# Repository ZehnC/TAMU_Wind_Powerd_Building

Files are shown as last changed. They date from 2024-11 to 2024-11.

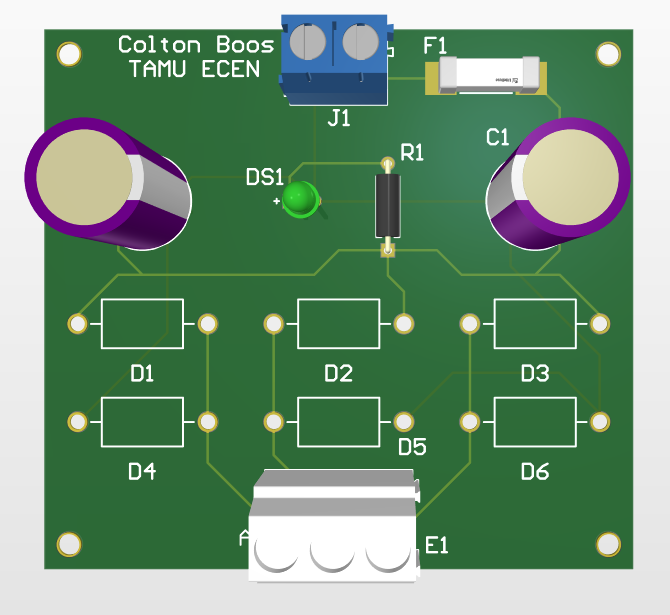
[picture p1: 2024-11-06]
RectifierPCB/rectifier_digital.PNG

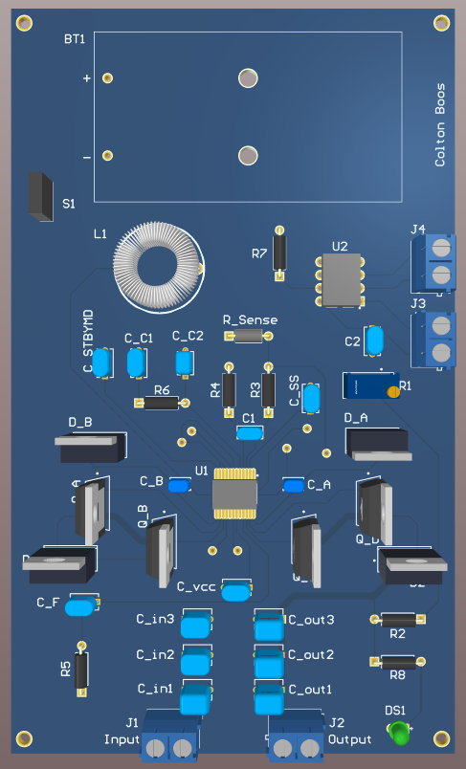
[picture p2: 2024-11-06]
BuckBoostConverterPCB/converter_digitalPCB.PNG

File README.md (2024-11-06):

# The-Wind-Powered-Building
Documentation and Files for the A&M Team 7 Wind-Powered-Building <br />
Team members include Colton Boos, Peter Zha, Reggie Sampson, and Maxwell Chen <br />
Sponsored by Dr. Wonhyeok Jang, with TA Rohith Ramanujam Kumar <br />

The wind-powered building is designed to deliver power from a small wind turbine to a residential home. The operation of the project consists of four main subsystems: the rectification and conversion subsystem, the switch controller subsystem, the inversion and conversion subsystem, and the monitor subsystem. These four systems working together converts three phase AC power to be stored in two batteries as DC power, which is then delivered to AC and DC loads. The amount of power generated and used is tracked by the monitor subsystem as well as battery capacity, and determines which battery to charge and which battery to discharge.
Due to issues with the wind turbine, our sponsor has given us approval to use an AC power supply as a substitute for demonstration. Hooking up the rectifier and converter to the input, the power input will be converted to DC power in order to charge the batteries. The microcontroller part of the monitor subsystem will automatically determine which battery needs to be charged. LED indicators inside the housing indicates which battery is charging and which battery is discharging. Power used from the batteries is delivered to two types of loads: an AC and DC load. The DC load is the LEDs mounted on the outside of the box. The AC load is directly next to the DC load, represented by a power outlet. The LEDs can be turned on and off and various loads can be plugged into the outlet.

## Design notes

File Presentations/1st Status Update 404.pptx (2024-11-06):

## Team 7: Wind-Powered Building Team Members: Colton, Reginald, Maxwell, Peter Sponsor: Dr. Jang TA: Rohith Ramanujam Kumar

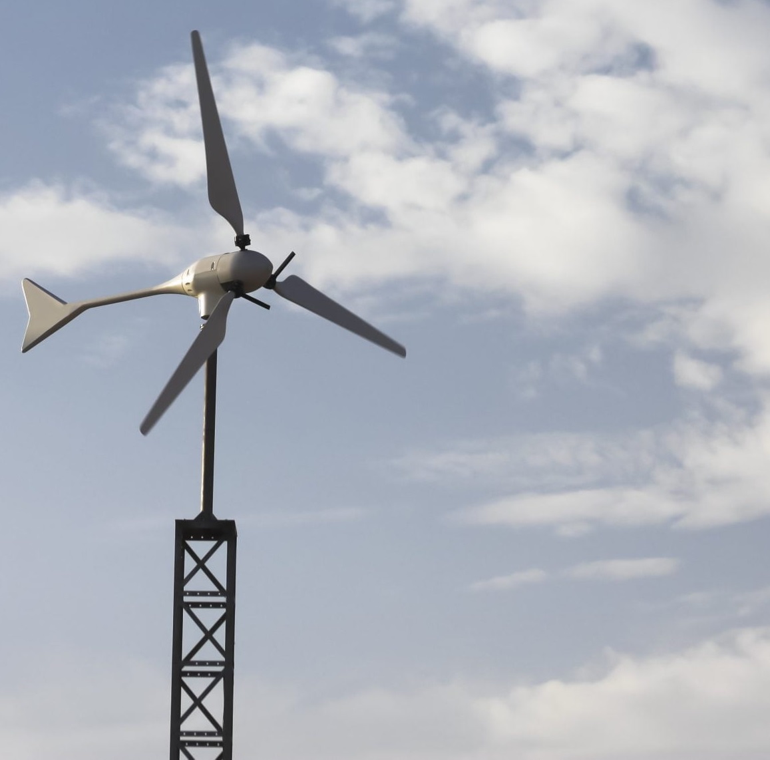
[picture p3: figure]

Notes: https://www.ryse.energy/3kw-wind-turbines/#iLightbox[gallery_image_1]/11

## Project Summary

- Implementing local renewable power generation to reduce reliance on fossil fuels
- Using a wind turbine to capture energy, store it in batteries, and power AC and DC loads

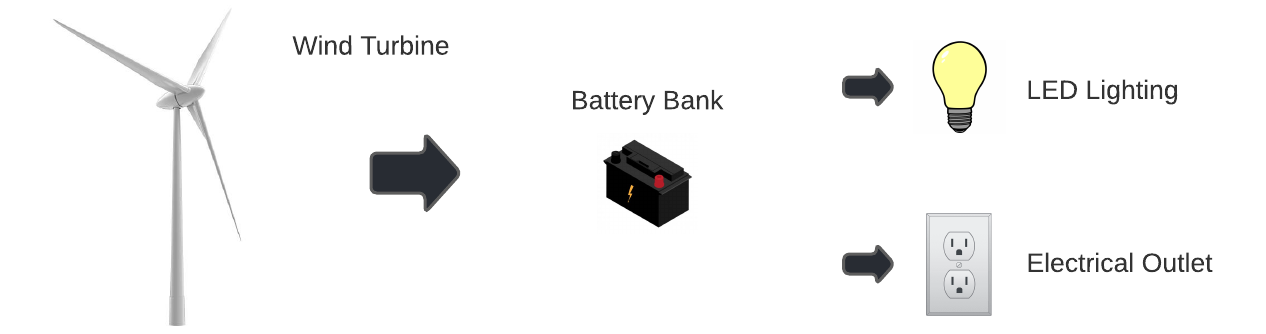
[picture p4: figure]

## Block Diagram and Task Partition

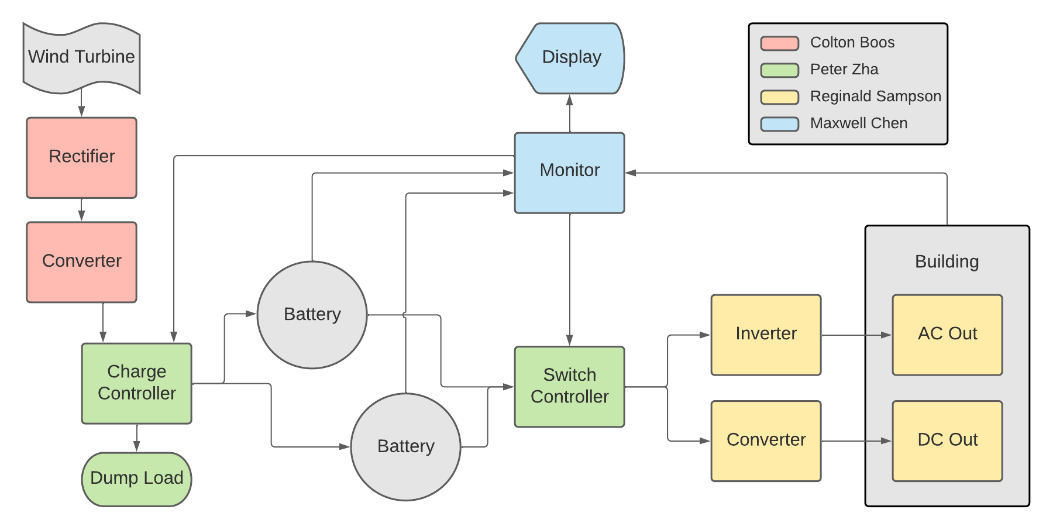
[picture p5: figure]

## Project Timeline

Early September 2022

Refine Subsystems

Ensure subsystems are in a working state and simulations are done.
Resolve any subsystem issues left over from the previous semester

Late September 2022

Begin Integration

All subsystems should be in complete working order.
Some PCBs and components/parts ordered and ready for soldering.

October 2022

Continue Integration and Validation

Continue and complete validation by no later than mid-October.

November 2022

Complete Validation

Final details and errors cleaned up. System should be completely validated and ready to present at showcase.

## Rectification and Conversion Subsystem Owner: Colton Boos

Accomplishments since 403 20 hours of effort | Ongoing progress/problems and plans until the next presentation
Finished simulations of buck-boost converter, utilizing a different IC from 403 Finished schematic and PCB design for rectifier | Finalize PCB design for buck-boost converter Start assembling components onto the rectifier PCB

## Rectification and Conversion Subsystem Owner: Colton Boos

Rectifier
- Same design from 403
- Using different components with higher voltage/current ratings for robustness


Buck-Boost Converter
- Output current depends on load resistance
- Need to add load resistor at the output

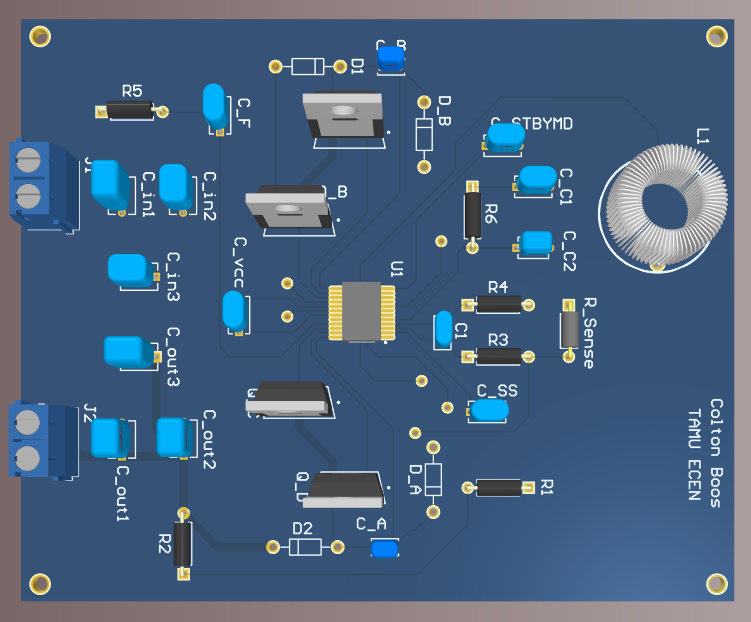
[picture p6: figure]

## Charge and Switch Controller Subsystem Owner: Peter Zha

Accomplishments since 403 15 hours of effort | Ongoing progress/problems and plans until the next presentation
Finished new design and simulations Finished determining possible battery switching cases | Need to do some physical validations Design and order PCBs

## Charge and Switch Controller Subsystem Owner: Peter Zha

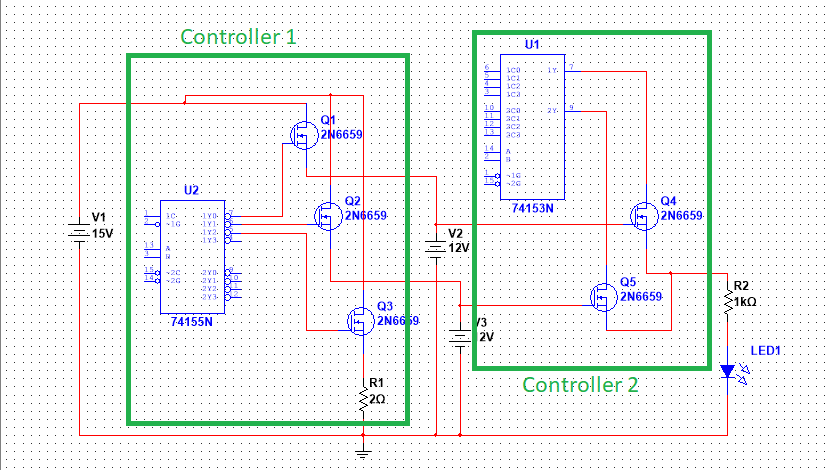
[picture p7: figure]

## Inversion and Conversion Subsystem Owner: Reginald Sampson

Accomplishments since 403 20 hours of effort | Ongoing progress/problems and plans until the next presentation
Finished rebuilding the Inverter and Converter with updated parts Finished schematic of Inverter and Converter designs | Finalize PCB design for Converter and Inverter No spice model exists for the LM2577 and CD4047 to simulate

## Inversion and Conversion Subsystem Owner: Reginald Sampson

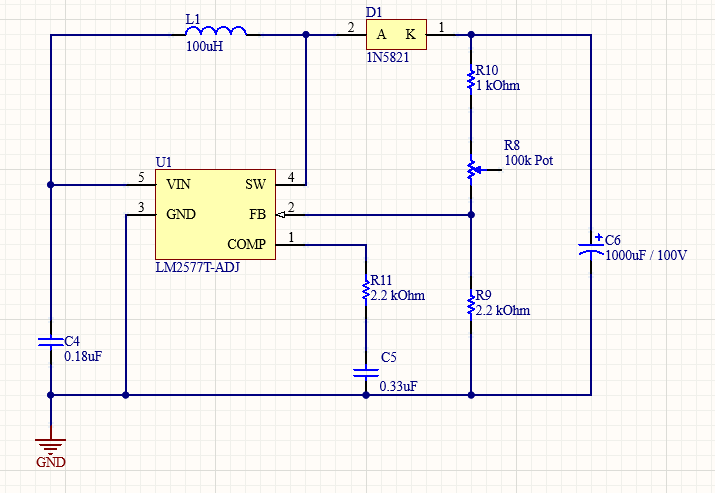
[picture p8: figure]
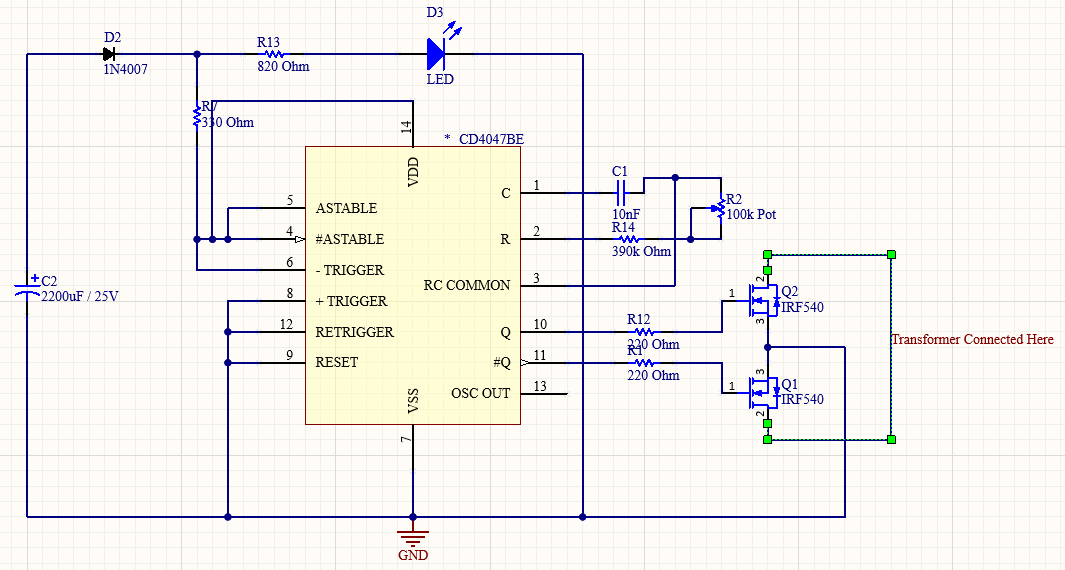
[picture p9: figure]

## Monitor Subsystem Owner: Maxwell Chen

Accomplishments since 403 10 hours of effort | Ongoing progress/problems and plans until the next presentation
Research on factors of Battery Health and Life Research on separate voltage and current sensors to use on the microcontroller | Integration of voltage and current sensors Implementation of Battery Health calculations onto the website through data gathered from the new sensors

## Monitor Subsystem Owner: Maxwell Chen

- State of Health can be used to determine our batteries health.
  - It can be described as the ratio of maximum battery charge to its rated capacity
- Will be utilizing a current sensor and decided to use a voltage sensor for better accuracy and safety

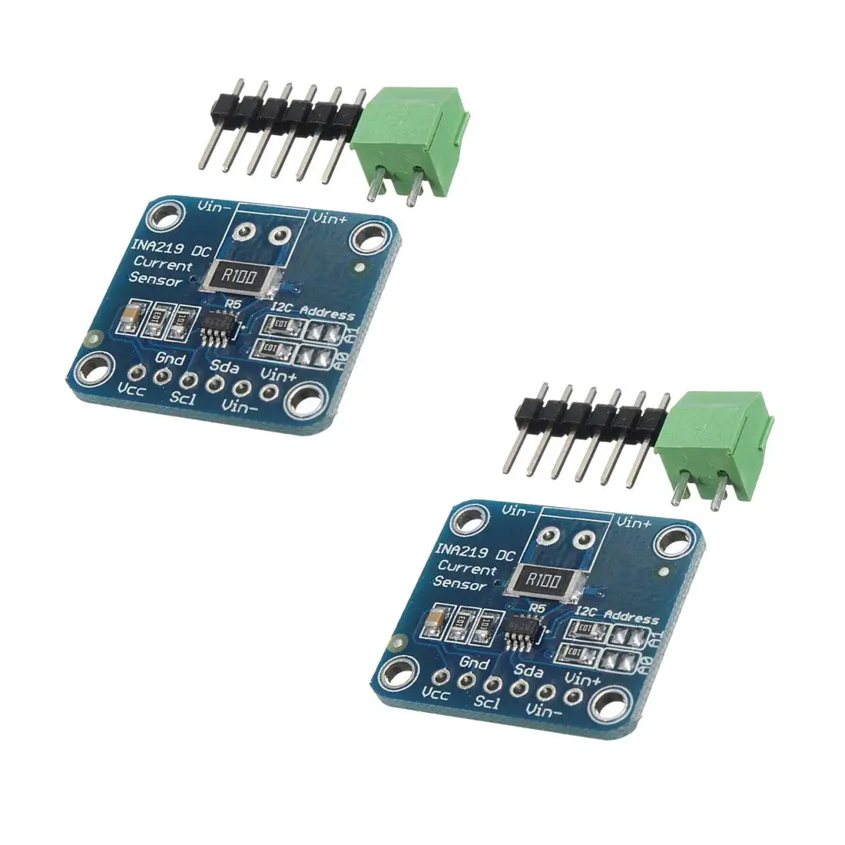
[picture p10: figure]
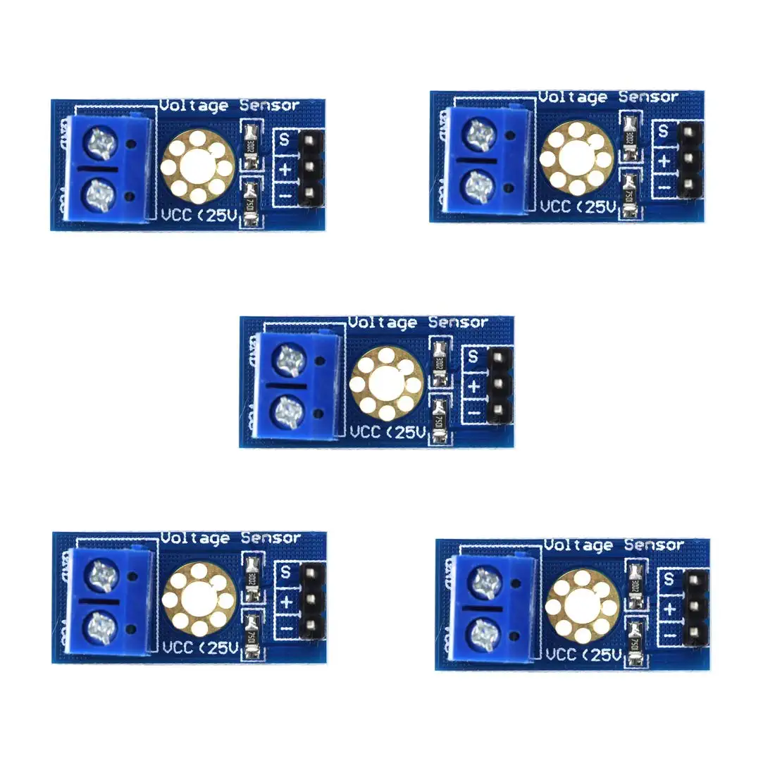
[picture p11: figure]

## Parts Ordering Status

Part Description | Status(Order Approved/ Order Placed/ Part Received
HiLetGo Voltage Sensor | Pending Approval
INA219 Current Sensor | Pending Approval
Power MOSFETs | Pending Approval
Rectifier PCB | Order Placed

## Execution & Plan

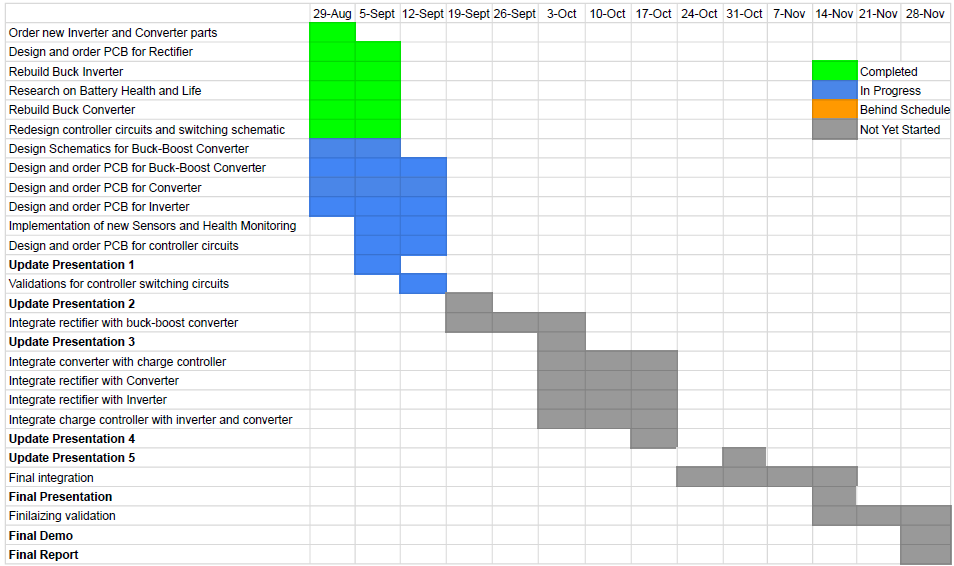
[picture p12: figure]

## Thank you for listening

Any Questions?

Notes: https://www.ryse.energy/3kw-wind-turbines/#iLightbox[gallery_image_1]/11

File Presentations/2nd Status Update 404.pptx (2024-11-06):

## Team 7: Wind-Powered Building Team Members: Colton, Reginald, Maxwell, Peter Sponsor: Dr. Jang TA: Rohith Ramanujam Kumar


2nd Status Update

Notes: https://www.ryse.energy/3kw-wind-turbines/#iLightbox[gallery_image_1]/11

## Project Summary

- Implementing local renewable power generation to reduce reliance on fossil fuels
- Using a wind turbine to capture energy, store it in batteries, and power AC and DC loads


## Block Diagram and Task Partition

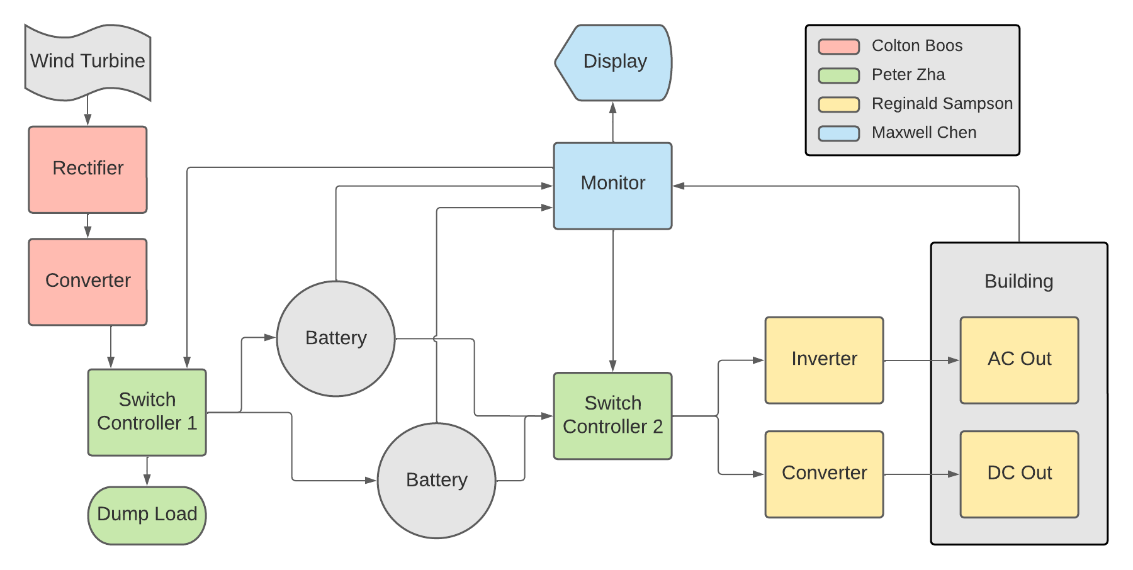
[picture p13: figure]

## Project Timeline

Early September

Refine Subsystems

Ensure subsystems are in a working state and simulations are done.
Resolve any subsystem issues left over from the previous semester.

Done

Late September

Begin Integration

All subsystems should be in complete working order with PCBs on the way.
Begin integrating rectifier with boost converter.

Early October

Continue Integration

All other PCBs should be ordered and ready to integrate.
Integrate Switch controllers with monitor subsystem.

In Progress

Late October

Continue Integration and Validation

Integration of Rectification and Conversion Subsystem with Switch Controller 1

Behind Schedule

Late October

Continue Integration and Validation

Integration of Inversion and Conversion Subsystem with Switch Controller 2

Late November

Complete Validation

Complete and document final validation tests for final report and presentation.

Not Started

## Rectification and Conversion Subsystem Owner: Colton Boos

Accomplishments since last review 15 hours of effort | Ongoing progress/problems and plans until the next presentation
Finished PCB design for buck-boost converter and placed order | Finish soldering components onto rectifier and converter PCBs Validate they’re both working independently Begin integration of both circuits

## Rectification and Conversion Subsystem Owner: Colton Boos


Buck-Boost Converter
- Output voltage depends on feedback resistor
- For charging batteries, there are different charging methods available
- Currently planning to implement constant voltage charging with analog resistor
- Added functionality for digital potentiometer for constant current charging

## Switch Controller Subsystem Owner: Peter Zha

Accomplishments since last review 10 hours of effort | Ongoing progress/problems and plans until the next presentation
Fixed newfound errors in simulation and design Nearly complete PCB designs | Finish up and order PCBs Physical validations on breadboard while waiting for PCBs Begin integrating

## Switch Controller Subsystem Owner: Peter Zha

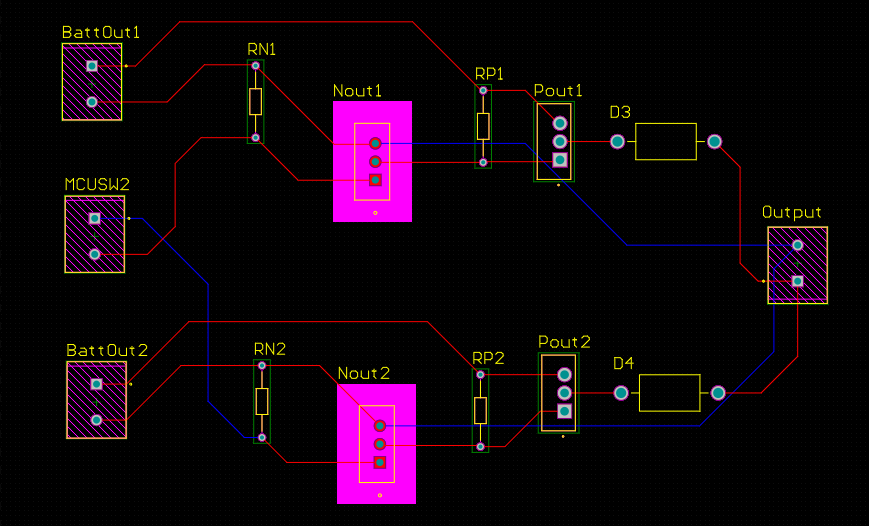
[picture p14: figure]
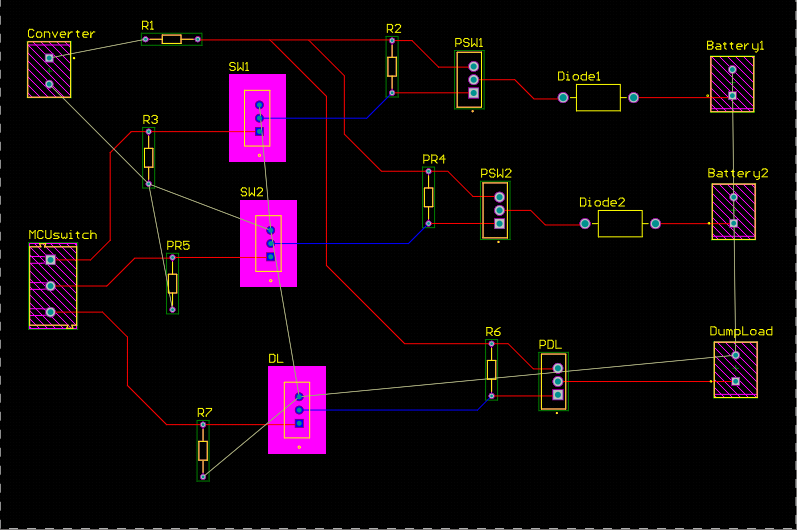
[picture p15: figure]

## Inversion and Conversion Subsystem Owner: Reginald Sampson

Accomplishments since last review 10 hours of effort | Ongoing progress/problems and plans until the next presentation
Validated the rebuilt converter and inverter breadboard circuits Designed converter and inverter PCBs Began reconstruction of physical network connecting to the loads | Get feedback from Dr. Lusher on PCB designs Order PCBs

## Inversion and Conversion Subsystem Owner: Reginald Sampson

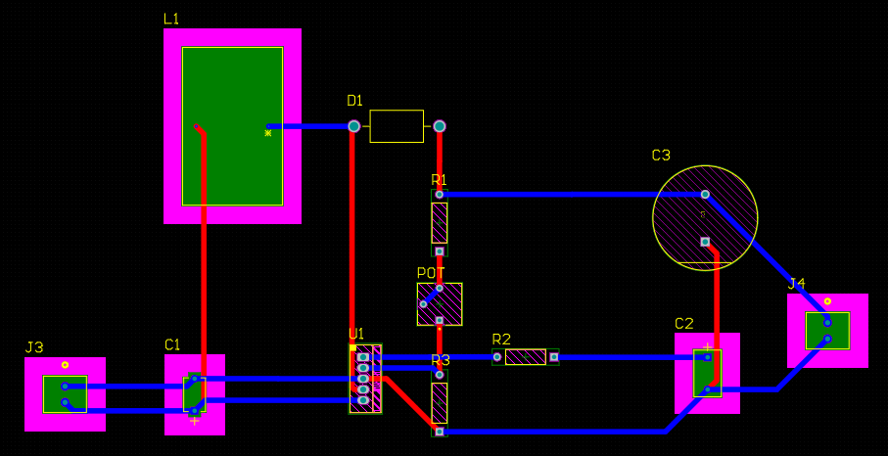
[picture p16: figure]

Converter

Inverter

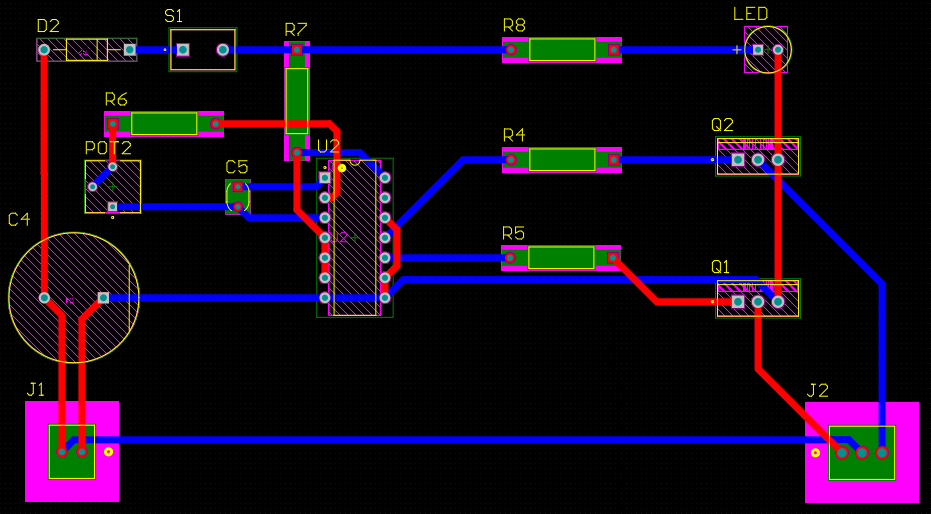
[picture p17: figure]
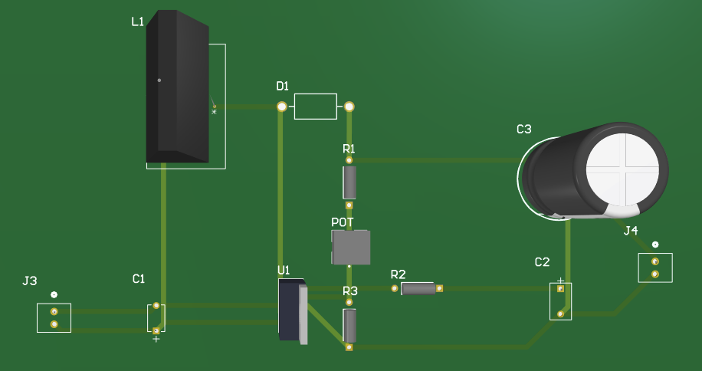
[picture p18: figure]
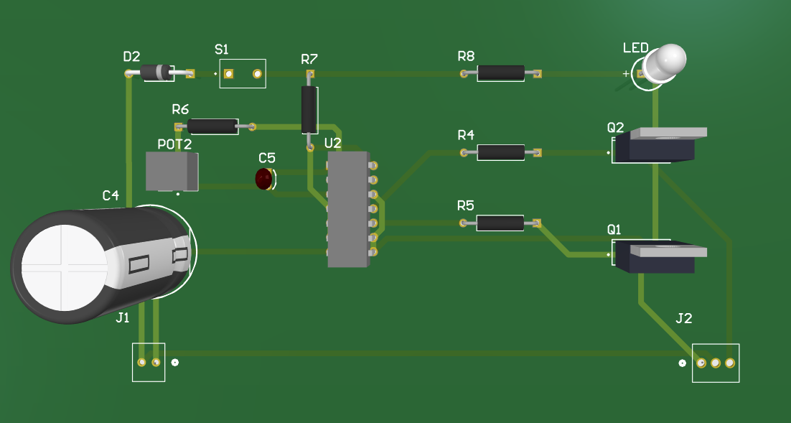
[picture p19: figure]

## Monitor Subsystem Owner: Maxwell Chen

Accomplishments since last review 8 hours of effort | Ongoing progress/problems and plans until the next presentation
Working on code for the current sensors and implementation of Battery Health Research and discussion with team members on optimal battery charging | The new sensors were delayed and did not arrive last week Continue working on code and implementing the sensors this week along with testing if possible

## Monitor Subsystem Owner: Maxwell Chen

- Flow Chart for battery switching logic

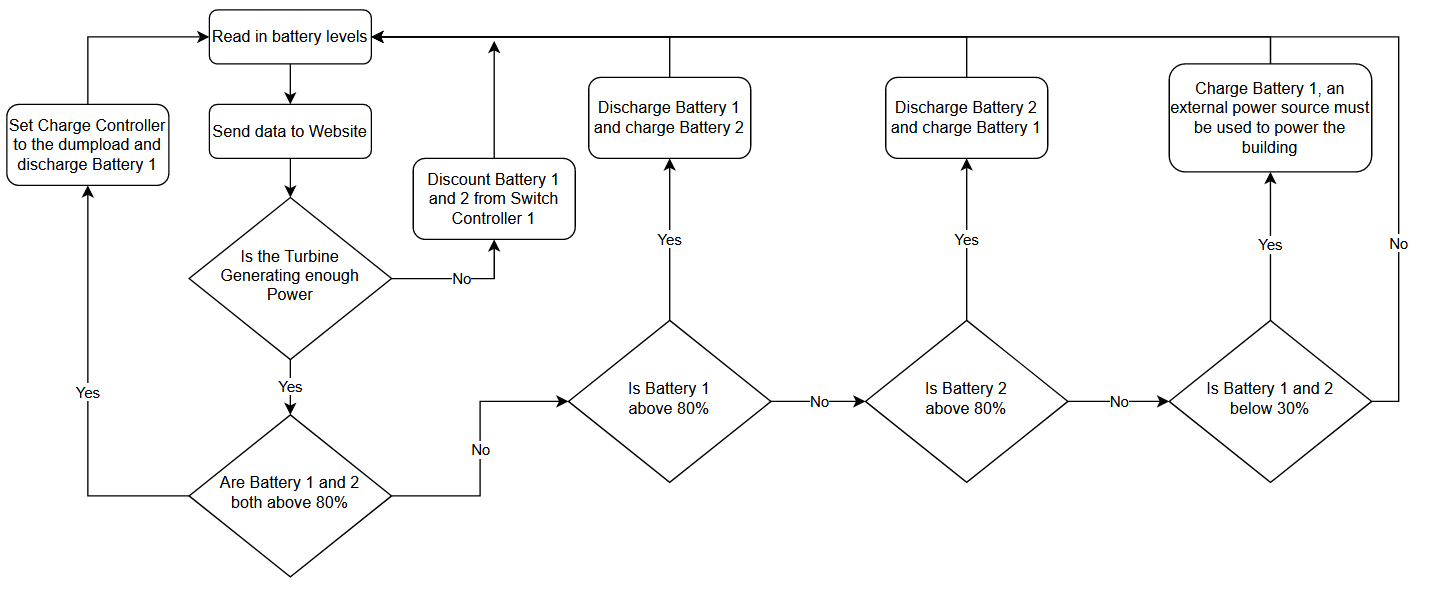
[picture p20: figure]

## Parts Ordering Status

Part Description | Status(Order Approved/ Order Placed/ Part Received
HiLetGo Voltage Sensor | Parts Received
INA219 Current Sensor | Parts Received
Power MOSFETs | Parts Received
Rectifier PCB | Order Received
Converter PCB | Order Placed

## Execution & Plan

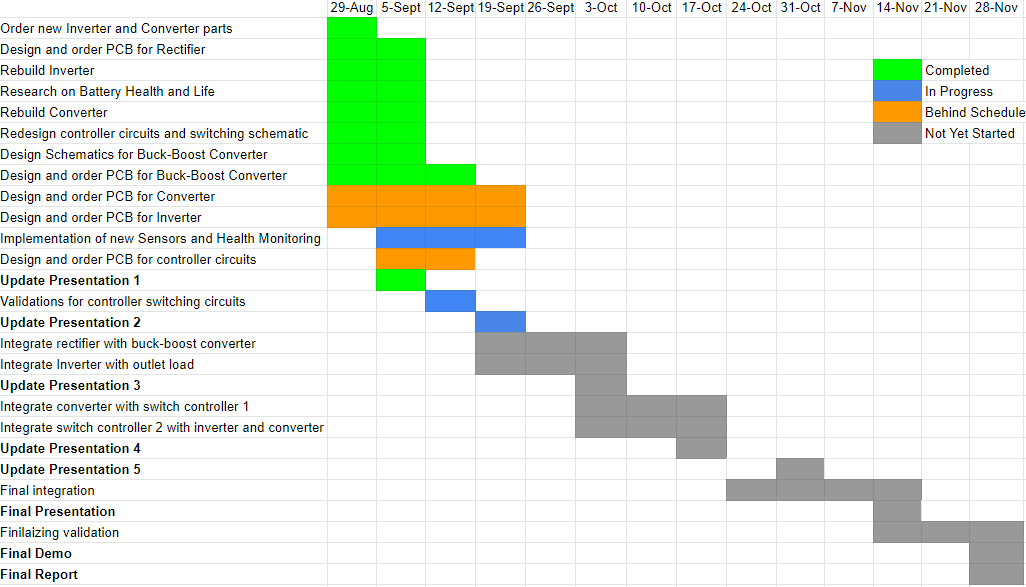
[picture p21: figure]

## Thank you for listening

Any Questions?

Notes: https://www.ryse.energy/3kw-wind-turbines/#iLightbox[gallery_image_1]/11

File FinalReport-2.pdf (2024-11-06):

Concept of Operations | Revision - 1
Wind-Powered Building

# Wind-Powered Building

# Reginald Sampson Maxwell Chen Colton Boos Peter Zha

# CONCEPT OF OPERATIONS

Concept of Operations | Revision – 1

### REVISION – 1 12 February 2022

Concept of Operations | Revision - 1

I

### CONCEPT OF OPERATIONS

### FOR

## Wind-Powered Building

TEAM 07

APPROVED BY:

Colton Boos | 04/30/22
Project Leader | Date

_____________________________
Prof. Kalafatis | Date

_____________________________
T/A | Date

Concept of Operations | Revision - 1

II

### Change Record

Rev. | Date | Originator | Approvals | Description
Draft | 2/9/2022 | Peter Zha | | Draft Release
1 | 2/12/2022 | Colton Boos | | Revision 1

Concept of Operations | Revision - 1

III

### Table of Contents

Table of Contents | III
List of Figures | IV

Concept of Operations | Revision - 1

IV

### List of Figures

Concept of Operations | Revision - 1

## 1. Executive Summary

Tall buildings, offices, and high-rises are commonplace in urban environments. In particular, strong winds can be found at the top of these structures, which is usually left unharvested. Our aim is to harness the power of the wind and take advantage of this form of energy that is readily available to us. Through The Wind-Powered Building, we will implement electricity generation at a local level. By powering part of the building’s electrical systems with renewable energy, this will save money for electricity producers and consumers, along with helping preserve the environment around us.

## 2. Introduction

The Wind-Powered Building will harness mechanical energy from the wind and convert it into electrical energy. By integrating a wind turbine into the building’s structure, the electrical energy produced will shed part of the electrical load a building consumes. This results in a reduced usage of fossil fuels and a step towards using only renewable energy sources for the future of the environment.

### 2.1. Background

Buildings receive their power through the electrical grid, and typically electricity generation is produced from fossil fuels. While the electrical grid does implement renewable energy sources for some electrical generation, it is not enough. Coal is the largest source of electrical generation as well as the biggest contributor to climate change [1]. Furthermore, wind power is commonly captured through large scale wind farms, which may consist of hundreds of individual wind turbines. Wind farms, in addition to other forms of electricity production, are typically at remote locations and their power is carried by transmission lines to higher density populations [2].

By implementing wind-power closer to the consumer, there is no transmission network involved. Additionally, with this method of power generation, wind turbines will be able to take part of the building’s electrical load off the grid, and away from nonrenewable fossil fuels.

### 2.2. Overview

Our system will be deployed to capture wind energy on the top of a building, and in turn, deliver power to that same building. Power will be stored into battery reserves and be used immediately as well as for the future. In cases of when the battery is full there will be a charge controller to change the flow of power onto a dump load. A system of power conversions will be implemented on the input and output of the battery to deliver power to the building.

A monitoring system will also be set up to observe the power intake and outtake of our wind powered system. The monitoring system will be able to display the status of the batteries and assist in tasks such as changing the flow of power to the batteries or the dump load.

Concept of Operations | Revision - 1

### 2.3. Referenced Documents and Standards

[1] J.M.K.C. Donev et al. (2021). Energy Education - Electrical generation [Online]. Available: https://energyeducation.ca/encyclopedia/Electrical_generation.
[2] F. Blaabjerg and K. Ma, "Wind Energy Systems," in Proceedings of the IEEE, vol. 105, no. 11, pp. 2116-2131, Nov. 2017, doi: 10.1109/JPROC.2017.2695485.
[3] “Design and Construction of a Wind Turbine Dump-Load Charge Controller.” Warlock, Warlock Engineering, https://www.warlock.com.au/dumploadcontroller.htm.
[4] Analyst, James Gignac Lead Midwest Energy, et al. “Wind Turbine Blades Don't Have to End up in Landfills.” The Equation, Union of Concerned Scientists, 7 Dec. 2021, https://blog.ucsusa.org/james-gignac/wind-turbine-blades-recycling/.
[5] “Wind Turbine Dump and Diversion Loads: What They Do and How to Choose the Right System.” Windy Nation, https://www.windynation.com/jzv/inf/wind-turbine-dump-anddiversion-loads-what-they-do-and-how-choose-rights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 oltage%20
of%20the%20battery%20bank.&text=Once%20the%20battery%20bank%27s%20vol ta ge,to%20charging%20the%20battery%20bank.
[6] “Charge Controller.” The Back Shed, https://www.thebackshed.com/windmill/articles/TL084-Controller.asp.
[7] “How To Charge a Lead Acid Battery” Power Sonic https://www.power-sonic.com/blog/how-to-charge-a-lead-acid-battery/

Concept of Operations | Revision - 1

## 3. Operating Concept

### 3.1. Scope

The Wind-Powered Building will consist of an outlet for distributing and deploying power for appliances. While the entire system is a scaled down version of large wind turbines connected to the power grid, our system will charge battery storages instead. The wind turbine used will be pre-assembled and will not be part of the components designed for the project. Subsystems connected to the wind turbine will be designed and fabricated to control the power output generated by the wind turbine and power input into the building. An additional subsystem will monitor, control, and display further aspects of The Wind-Powered Building.

### 3.2. Operational Description and Constraints

The Wind-Powered Building will be used to power basic electrical loads that plug into AC, as well as lighting systems that run off DC. The AC power output into the building will imitate a standard electrical outlet in a residential home, therefore, voltage, current, and power readings will be compared with that of a typical home outlet. The turbine itself will be chosen as an individual unit designed to power small appliances, including:
- Laptop and cellphone chargers
- Small monitors
- LED Lighting

Small household appliances will benefit the most from the system, as they draw a smaller amount of power from the battery. When maximum charge of the batteries is reached, the dump load drawing power away from batteries must be sufficiently large enough to consume all power produced by the wind turbine. Due to the limited budget of $400, additional batteries may not be available to substitute for a dump load. There will be a limited amount of power generated due to the costs of the wind turbine and batteries. The Wind-Powered Building will only be tested under windy conditions. The use of artificial wind by fans shall be used to simulate these testing conditions as well.

### 3.3. System Description

The Wind-Powered Building consists of five key subsystems, with four of these involving power conversion and delivery. The wind turbine will generate power and deliver this to a battery bank. The battery bank will deliver power to the building, including alternating current and direct current. The bulk of our subsystems lies within this flow of power from the source to the destination.

Rectification and Conversion Subsystem: The wind turbine will output three-phase alternating current (AC). However, direct current (DC) is needed to charge the battery bank. The rectifier will take the wind turbine’s AC and output DC. The converter will take this DC voltage and convert it to a DC voltage appropriate to the batteries’ specification for charging.

Concept of Operations | Revision - 1

Inversion and Conversion Subsystem: The batteries will output DC and after this, the power will split into separate paths for use in the building. The first path involves the use of an inverter to take the DC from the battery and output AC. This can be used in the building to power AC loads. The second path will lead to the building’s lighting system which requires the use of DC. To achieve the specific voltage used by the lighting system, the converter will take the batteries’ power output and convert it to that specified DC voltage.

Charge and Switch Controller Subsystem: The charge controller comes before the battery bank where it changes the flow of power from one battery to the other. After one battery is fully charged, the charge controller will automatically start charging the other battery. The charge controller also serves as a safety measure for the batteries. When both batteries are fully charged, the charge controller will divert electricity to a dump load. It is not safe or efficient to continue charging a full battery, and it is important for the wind turbine to always have an electrical load connected.

The switch controller comes after the battery where it utilizes the proper flow of power. The switch controller automatically connects the appropriate battery to the inverter and converter. While one battery is charging, the switch controller will connect the other battery to the building. Its job is to prevent the simultaneous charging and discharging of one battery.

Monitor Subsystem: The monitor is the central intelligent hub of the Wind-Powered Building, and it serves two major functions. The first is the collection and display of data. By collecting the building’s power consumption and status of the battery bank charge levels, we can output this on a website. The second function involves the use of this data to control aspects of The Wind-Powered Building. Since the monitor will read the batteries’ charge levels, it will send appropriate signals to the controller. The monitor is programmed to read states of the charge controller, and this will determine the state of the switch controller.

Concept of Operations | Revision - 1

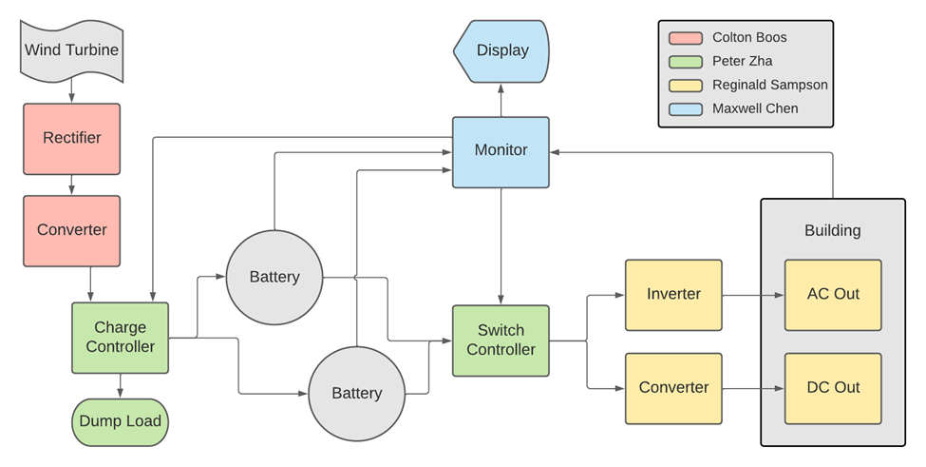
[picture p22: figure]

### 3.4. Modes of Operations

Charging: The charging mode features two processes involving the battery bank. While a battery is being charged through the wind turbine, it shall not be connected to any electrical load. The Wind-Powered Building shall be supplied by the battery not being charged. For example, when the first battery is being charged, the second battery will provide power to the building. The charge and switch controllers are managing this flow of power.

Fully Charged: When the battery bank is fully charged, the flow of electricity will be diverted away from these batteries. The charge controller will connect the power generated by the wind turbine to a dump load. In this mode, The Wind-Powered Building shall continue consuming power if needed and once the battery drops below a specified threshold, the mode will change back to charging.

### 3.5. Users

Individual consumers and larger entities will equally benefit from The Wind-Powered Building. In smaller applications and residential use, the wind turbine may provide adequate power to allow off-grid use, especially in conjunction with those already using alternative methods such as solar power. In larger applications, the wind turbine may be added to a building with existing electrical grid connections. In both cases, installation of the wind turbine and sequential subsystems will require basic knowledge of power systems. The user must understand how to safely connect resistive loads and wire terminals, as well as how to interpret voltage and power readings.

Figure 1. Wind-Powered Building Block Diagram

Concept of Operations | Revision - 1

### 3.6. Support

Support for the users will be provided through manuals created by the team. Potential hazards and safety precautions will be clearly stated. Basic troubleshooting steps will also be listed to provide users with solutions for common issues found within each subsystem.

Concept of Operations | Revision - 1

## 4. Scenario(s)

### 4.1. Renewable Energy

Areas with emission standards may be looking for renewable energy sources to reduce their emissions of CO2 and greenhouse gasses. The Wind-Powered Building will generate electric power by harnessing wind and utilizing a renewable energy. Wind is an infinite source of fuel and is only limited by the capacity of the battery used to store the power generated.

### 4.2. Optimizing Cost of Energy

Buildings that require expensive fuel sources or experience high power losses may need a new cost-effective system to generate power. The Wind-Powered Building will harness wind, a free fuel source, to generate its power. The cost saved in the long term will pay for the initial construction of the wind turbine system and on-going maintenance of the system. Additionally, The Wind-Powered Building will monitor its power usage and switch between wind and grid generated power.

### 4.3. Independent Power Source

Remote geographical regions may be dependent on imported fuel sources to generate power to their buildings. The Wind-Powered Building will focus on using wind as a local and independent fuel source. Usage of nearby sources of energy will not only decrease costs, with less reliance on importing fuel, but also help promote environmentally friendly operations.

Concept of Operations | Revision - 1

## 5. Analysis

### 5.1. Summary of Proposed Improvements

The Wind-Powered Building aims to bring an alternative source of energy in a changing time where more people are moving towards renewable energy sources. Wind-generated energy seeks to replace fossil fuel-based energy sources, and the Wind-Power Building serves as a model for future renewable energy solutions. The project places greater emphasis on tweaking individual subsystem components for better performance overall, leading to more efficient and sophisticated wind-powered systems.

### 5.2. Disadvantages and Limitations

The complete Wind-Powered Building will be limited by operational capacity and battery requirements. Subsystem components cannot exceed maximum capacity requirements for voltage, current, power, and energy consumption [3]. Overcharging the battery for long periods of time can result in permanently reduced battery capacity [4]. The wind turbine will not output power in times where there is no wind. The battery will provide needed power during this time. In times where there is no wind and the battery is drained, the building and its systems will be powered by the grid.

### 5.3. Alternatives

There are a few different configurations for the Wind-Powered Building. The location of the wind turbine can be varied by placing it lower on the building, or even placing it on the ground. However, because stronger winds are located at higher elevations, this solution could raise problems for this alternative. Wind turbines that are placed lower will lead to more intermittency of power generation in conjunction with less overall power output. A different alternative would be increasing wind power generation to provide more power to the building and decreasing the load to the grid. Larger energy storages and bigger wind turbines are needed with this approach, but battery banks are resource intensive and would also require higher initial costs to set up.

### 5.4. Impact

Providing renewable energy through wind power has considerable benefits to our environment; however, there are some drawbacks to consider. Wind turbines can cause noise pollution due to its mechanical system, and they can be a visual nuisance as well. Additionally, they can harm local wildlife, including birds and bats that fly into spinning turbine blades. Wind turbines can have a long lifespan, but when they are decommissioned, their blades will need to be recycled and reused, or risk filling up landfills even more [5]. Routine maintenance will be required in frequent intervals to keep the turbines optimized.

Functional System Requirements | Revision - 1

# Wind-Powered Building

# Reginald Sampson Maxwell Chen Colton Boos Peter Zha

# FUNCTIONAL SYSTEM REQUIREMENTS

### REVISION – Draft 22 February 2022

Functional System Requirements | Revision - 1

I

### FUNCTIONAL SYSTEM REQUIREMENTS

### FOR

## Wind-Powered Building

PREPARED BY:

_____________________________
Author | Date

APPROVED BY:

Colton Boos | 04/30/22
Project Leader | Date

_____________________________
John Lusher, P.E. | Date

_____________________________
T/A | Date

Functional System Requirements | Revision - 1

II

### Change Record

Rev. | Date | Originator | Approvals | Description
Draft | 02/22/2022 | Colton Boos | | Draft Release
1 | 04/30/2022 | Colton Boos | | Revision 1

Functional System Requirements | Revision - 1

III

### Table of Contents

Table of Contents | III
List of Tables | IV
List of Figures | V

Functional System Requirements | Revision - 1

IV

### List of Tables

Functional System Requirements | Revision - 1

V

### List of Figures

Functional System Requirements | Revision - 1

## 1. Introduction

### 1.1. Purpose and Scope

The Wind-Powered Building is a new power system designed to be an easy way for people to integrate the power of wind energy into their buildings, reducing the usage of fossil fuels and promoting the usage of green energy. Our system is designed to be quite simple to allow for implementation into a variety of buildings. It has also been designed in a fashion that will allow the user to easily monitor the system. Figure 1 shows a general outline of the system with its various components.

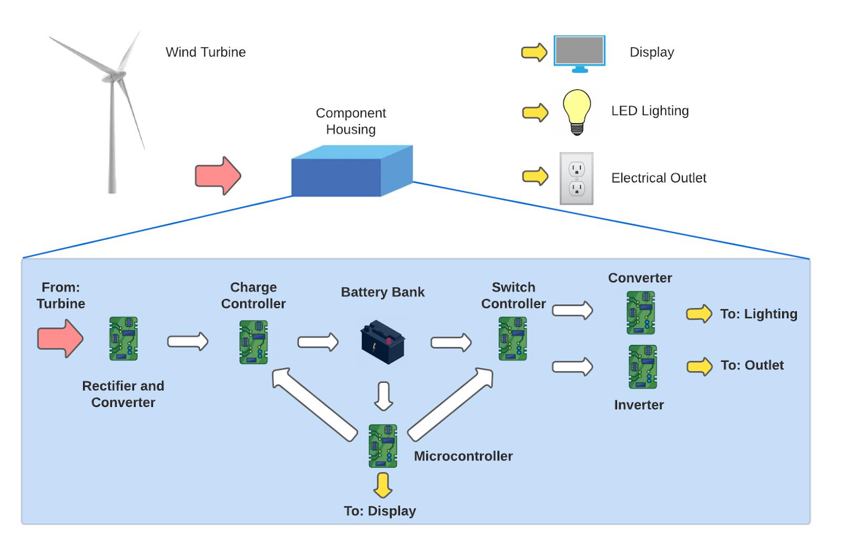
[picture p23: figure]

Figure 1. Wind-Powered Building Conceptual Implementation

The system converts energy generated by the wind turbine into usable energy for the building. This is achieved through the usage of a rectifier and converter to convert and lower the power into usable state to be stored in the batteries. Once the energy is stored in the battery it is then sent to be used by the building with an inverter and converter to convert the power into either AC or DC power based on the appliances used by the building.

The system also has a monitoring system that will track the battery levels of both batteries. Using this information, the monitoring system will then manage the switch controllers to control which battery is being used and which battery is being charged. This includes the small chance that both batteries are fully charged in which case the dumpload will be

Functional System Requirements | Revision - 1

utilized as a safety measure. In addition to these functions the monitoring system will also be able to provide useful information to the user such as power generated by the wind turbine and the power consumption of the building on the entire system.

### 1.2. Responsibility and Change Authority

The team leader, Colton Boos will hold the responsibility of ensuring that the project requirements are met. The project sponsor, Wonheok Jang and team leader, Colton Boos possess the authority to make changes to the specifications and requirements of the system.

Subsystem | Responsibility
Rectification and Conversion | Colton Boos
Inversion and Conversion | Reggie Sampson
Charge and Switch Controller | Peter Zha
Monitor System | Maxwell Chen

Table 1. Subsystem Ownership

Functional System Requirements | Revision - 1

## 2. Applicable and Reference Documents

### 2.1. Applicable Documents

The following documents, of the exact issue and revision shown, form a part of this specification to the extent specified herein:

Document Number | Revision/Release Date | Document Title
IEEE 2760 | 2020 | IEEE Guide for Wind Power Plant Grounding System Design for Personal Safety
IEEE 2030.2.1 | 2019 | IEEE Guide for Design, Operation, and Maintenance of Battery Energy Storage Systems, both Stationary and Mobile, and Applications Integrated with Electric Power Systems
IEEE 1834 | 2019 | IEEE Standard for Technology Supervision Code for Wind Turbine Rotor Systems
IEEE 60076-16 | 2018 | IEC/IEEE International Standard - Power transformers - Part 16: Transformers for wind turbine applications
IEEE C57.12.01 | 2020 | IEEE Standard for General Requirements for Dry-Type Distribution and Power Transformers
NEC 210 | 2020 | National Electrical Code, Branch Circuits

### 2.2. Reference Documents

The following documents are reference documents utilized in the development of this specification. These documents do not form a part of this specification and are not controlled by their reference herein.

Document Number | Revision/Release Date | Document Title
IEEE C37.30.2 | 2015 | IEEE Guide for Wind-Loading Evaluation of High Voltage (>1000V) Air-Break Switches

### 2.3. Order of Precedence

In the event of a conflict between the text of this specification and an applicable document cited herein, the text of this specification takes precedence without any exceptions.

All specifications, standards, exhibits, drawings or other documents that are invoked as “applicable” in this specification are incorporated as cited. All documents that are referred to within an applicable report are considered to be for guidance and information only, except ICDs that have their relevant documents considered to be incorporated as cited.

Functional System Requirements | Revision - 1

## 3. Requirements

### 3.1. System Definition

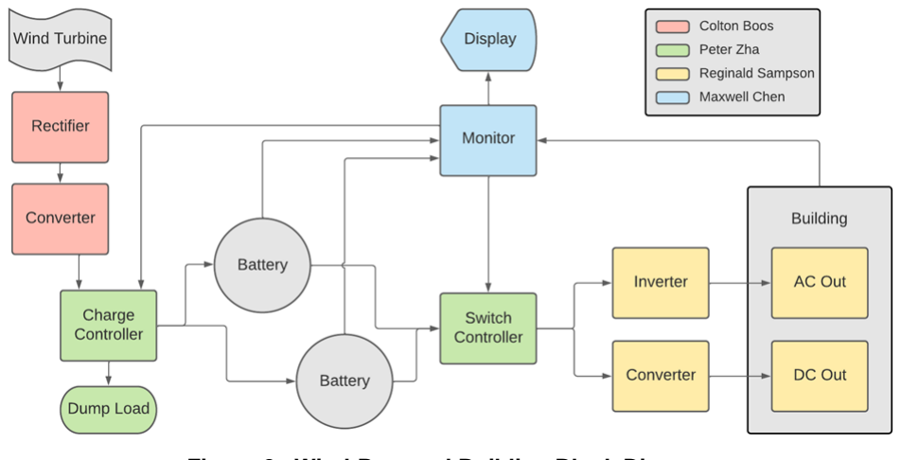
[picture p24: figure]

Figure 2. Wind-Powered Building Block Diagram

The Wind-Powered Building will be supplied by electricity through this flow of power. The wind turbine will generate power and store this into the battery bank. One subsystem is involved in this path. Rectification and Conversion subsystem will convert power to meet the batteries’ specifications. After this, the battery will supply power to the building with another subsystem involved in this path. Conversion and Inversion subsystem will convert the batteries’ power into DC and AC respectively. A switching subsystem will be in place before and after the battery bank. This is in charge of what battery to charge and what battery to power the building. Separately, a Monitor subsystem will observe the batteries’ charge and power consumption of the building, and display the information onto a website.

### 3.2. Characteristics

### 3.2.0. Functional / Performance Requirements

### 3.2.0.1. Energy Storage

The Wind-Powered Building shall take the energy produced by the wind turbine and store this into the battery bank. The system shall charge two batteries, each with 7Ah capacity.

Rationale: Due to the nature of wind power being intermittent, energy storage is needed to provide the building with constant electricity, including periods the wind turbine may go without producing power.

Functional System Requirements | Revision - 1

### 3.2.0.2. Power Output

The Wind-Powered Building shall provide two forms of electrical output: AC and DC. Further details are elaborated in Electrical Characteristics below.

Rationale: This is the core system performance requirement. The Wind-Powered
Building will provide two different forms of electrical output, AC and DC, due to how different appliances in the building require either AC or DC power.

### 3.2.0.3. Frequency of Measurement

The Wind-Powered Building monitoring system checks the status of the battery every couple of seconds to ensure it has an accurate reading.

Rationale: The monitoring system should be consistently checking the status of the battery in order to ensure that the batteries are not going over capacity or that there is no power source to output to the building.

### 3.2.1. Physical Characteristics

### 3.2.1.1. Mass

The mass of the wind turbine shall not exceed individual building safety standards in regards to rooftop appliances.

Rationale: The wind turbine should not damage the roof of the structure supporting it, and likewise must have a stable foundation on which to stand.

### 3.2.1.2. Structure

A majority of the components will be internal inside the building however the wind turbine needs to be securely placed on the building.

Rationale: The wind turbine will be susceptible to the various weather conditions so it
needs to be placed securely in order to ensure that any incidents do not occur.

### 3.2.1.3. Mounting

The Wind-Powered Building and all its subsystems properly mounted shall be captured in the Wind-Powered Building ICD.

Rationale: Properly mounted subsystems of the Wind-Powered Building and their connections include thermal and electrical components.

Functional System Requirements | Revision - 1

### 3.2.2. Electrical Characteristics

### 3.2.2.1. Inputs

a. The presence or absence of any combination of the input signals in accordance with ICD specifications applied in any sequence shall not damage the Search and Rescue System, reduce its life expectancy, or cause any malfunction, either when the unit is powered or when it is not.
b. No sequence of command shall damage the Search and Rescue System, reduce its life expectancy, or cause any malfunction.

Rationale: By design, should limit the chance of damage or malfunction by
user/technician error.

### 3.2.2.1.1. Power Production

a. The maximum peak power of the system shall not exceed 800 watts.

Rationale: This is measurement corresponds with the power output of the wind turbine to be connected with the combined subsystems.

### 3.2.2.1.2. Input Voltage Level for Rectification

The input voltage level for the rectification circuit of the Wind-Powered Building shall be 12V AC.

Rationale: The wind turbine will output a specified voltage, and this will feed directly into
the rectifier.

### 3.2.2.1.3. Input Voltage Level for Converter

The input voltage level for the converter circuits shall be +12V DC.

Rationale: Rectifier output voltage feeds into first converter, battery bank output voltage feeds into second converter, both consist of 12 volt DC.

### 3.2.2.1.4. Input Voltage for Battery Bank

Each battery shall be supplied with an input voltage of +15V DC for charging.

Rationale: Constraint due to the input voltage specified by the battery manufacturer for cyclic charging.

### 3.2.2.1.5. Input Voltage for Microcontroller

The input voltage for the microcontroller should not exceed +5V DC.

Rationale: Constraint due to the input voltage specified by the microcontroller manufacturer.

Functional System Requirements | Revision - 1

### 3.2.2.2. Outputs

### 3.2.2.2.1. Power Consumption

The power consumed by devices connected to the system shall not exceed 900 W

Rationale: Limited battery capacity cannot support higher power output.
Diagnostic Output

### 3.2.2.2.2. Inverter Voltage Output

The output voltage from the inverter connected to the building shall be equivalent to a nominal voltage of 120V RMS.

Rationale: A typical household outlet outputs 120 V, so the Wind-Powered Building should imitate this output when used to power household appliances.

### 3.2.2.2.3. Converter Voltage Output

The output voltage of the converter connected to the building shall be equivalent to +12VDC

Rationale: This is a constraint due to the input voltage for the LED lighting system used
in the building.

### 3.2.2.2.4. Display/Website Output

The Wind-Powered Building shall gather information on power consumption of the building as well as the charge levels of the battery bank and present this information on a website according to the Monitor subsystem.

Rationale: Includes information pertinent to users of the Wind-Powered Building.
Connectors

### 3.2.2.3. Wiring

The wiring for the Wind-Powered Building subsystem shall be completed according to NEC 210 standards.

Rationale: Conform to National Electrical Code standards for safe wiring.

Functional System Requirements | Revision - 1

### 3.2.3. Environmental Requirements

The Wind-Powered Building shall be designed to withstand and operate in the environments and laboratory tests specified in the following section.

Rationale: The Wind-Powered Building will need to function in outdoor environments due
to the nature of harnessing wind energy from a wind turbine.

### 3.2.3.1. Wind Speed

The Wind-Powered Building shall withstand and operate at wind speeds ranging from 5mph to 90mph.

Rationale: The wind turbine will need sufficient wind speed to output power while wind speeds too strong will contribute to the degradation of the wind turbine.

### 3.2.3.2. Altitude

The Wind-Powered Building shall withstand and operate at altitudes ranging from 20ft to 3,000ft compared to the altitude of ground level.

Rationale: Higher altitudes are associated with more turbulent winds which may contribute to the degradation of the wind turbine. Altitudes lower than 20ft compared to ground level is associated with lower wind speeds and insufficient power generation.

### 3.2.3.3. External Contamination

The Wind-Powered Building shall withstand and operate in environmental contamination such as smoke and smog. The system shall withstand and operate in environmental contamination such as dirt and dust excluding cases where extreme contamination causes the wind turbine to cease functioning properly. The system shall withstand and operate in environmental contamination such as wildlife and its corresponding interactions not including cases where the wind turbine may be damaged or impeded by wildlife.

Rationale: The Wind-Powered Building may be implemented in a variety of regions and the wind turbine must withstand and function in corresponding natural contaminations. For urban areas, smoke and smog are common contaminants. For more rural areas, dirt and dust are common contaminants. Both areas are associated with wildlife interactions.

### 3.2.3.4. Thermal

The Wind-Powered Building shall operate in temperatures ranging from -40°F to 120°F.

Rationale: This range includes the temperatures for a region where the customer may implement the Wind-Powered Building due to the operating temperature of the wind turbine.

### 3.2.3.5. Rain

The Wind-Powered Building shall withstand and operate in rain not exceeding 1” per hour.

Rationale: Extremely heavy rains may impede the production of sufficient power and will contribute to the degradation of the wind turbine and its blades.

Functional System Requirements | Revision - 1

### 3.2.4.6 Humidity

The Wind-Powered Building shall withstand and operate in humidity ranging from 0% to 90%

Rationale: Higher humidity is associated with faster corrosion of the wind turbine and will shorten the lifespan of the system.

Functional System Requirements | Revision - 1

## 4. Support Requirements

The Wind-Powered building does not require any extra resources or materials other than power to the monitoring system. The system will include a display to showcase information on the system such as the battery capacity, power generated, and power usage. As typical with any power system, the subsystems should be checked on and maintained regularly to ensure that they are functioning properly.

Functional System Requirements | Revision - 1

## Appendix A: Acronyms and Abbreviations

AC | Alternating Current
Ah | Ampere-hour
DC | Direct Current
Ft | Feet
LCD | Liquid Crystal Display
LED | Light-emitting Diode
mph | Miles per Hour
RMS | Root Mean Square
V | Volt
W | Watt

Functional System Requirements | Revision - 1

## Appendix B: Definition of Terms

Charge Controller | Mechanism used to control what battery is being charged and operation of the dump load.
Monitoring System | System that monitors the capacity of the battery along with the amount of power generated and used in the system
Switch Controller | Mechanism used to control what battery is being used by the building
Battery Bank | Composed of two 7.2Ah Sealed Lead-Acid Batteries

Interface Control Document | Revision - 1

# Wind-Powered Building

# Reginald Sampson Maxwell Chen Colton Boos Peter Zha

# INTERFACE CONTROL DOCUMENT

Interface Control Document | Revision - 1

### REVISION – 1 30 April 2022

Interface Control Document | Revision - 1

I

### INTERFACE CONTROL DOCUMENT

### FOR

## Wind-Powered Building

PREPARED BY:

_____________________________
Author | Date

APPROVED BY:

Colton Boos | 04/30/22
Project Leader | Date

_____________________________
John Lusher II, P.E. | Date

_____________________________
T/A | Date

Interface Control Document | Revision - 1

II

### Change Record

Rev. | Date | Originator | Approvals | Description
Draft | 02/22/2022 | Colton Boos | | Draft Release
1 | 04/30/2022 | Colton Boos | | Revision 2

Interface Control Document | Revision - 1

III

### Table of Contents

Table of Contents | III

Interface Control Document | Revision - 1

## 1. Overview

The Interface Control Document (ICD) for the Wind-Powered Building will provide more information on each of the four subsystems discussed in the Concept of Operations and the Functional Systems Requirements. The ICD will include specific information on the physical, thermal, electrical, and communication interfaces of the subsystems.

Interface Control Document | Revision - 1

## 2. References and Definitions

### 2.1. References

Heat Dissipation of the TriStar & TriStar MPPT Controllers inside Enclosures 2014

Safety Requirements for Board-Mounted DC/DC Converters
November 2011

### 2.2. Definitions

AC | Alternating Current
Cm | centimeter
LCD | Liquid Crystal Display
V | Volt

Interface Control Document | Revision - 1

## 3. Physical Interface

### 3.1. Weight

### 3.1.0. Weight of Inversion and Conversion Subsystem

The weight of the inversion and conversion subsystem shall be less than 2 pounds. Majority of the weight will be contributed by the PCB, heatsinks, a transformer and the three prong outlet.

### 3.1.1. Weight of Rectification and Conversion Subsystem

The weight of the rectification and conversion subsystem shall be no more than 1 pound. Both circuits consist of electrical components placed onto a PCB and by nature it will not be heavier than 1 pound.

### 3.1.2. Weight of Charge and Switch Controller Subsystem

The weight of each charge controller shall be within 1 to 3 pounds. Each charge controller consists of PCBs, heatsinks, switch relay solenoids, cooling fans, and the housing to protect the subsystem.

### 3.1.3. Weight of Monitor Subsystem

The weight of the monitor subsystem will only be a couple of grams as it is only composed of the microcontroller, internal wirings, and the housing for the system.

### 3.2. Dimensions

### 3.2.0. Dimension of Inversion and Conversion Subsystem

The dimensions of the inversion and conversion subsystem shall be 25 x 13 cm. These dimensions are the upper limit and may be subject to decrease if the PCB development requires less space or increase if a housing for the PCB is created.

### 3.2.1. Dimension of Rectification and Conversion Subsystem

The total area enclosed by the rectification and conversion subsystem shall be no bigger than 250cm² as the dimensions would be 25 x 10 cm. The subsystem can be decreased to a smaller dimension but it will not be bigger than proposed.

### 3.2.2. Dimension of Charge and Switch Controller Subsystem

The dimensions of each charge controller shall be approximately 30 x 12 x 7 cm in volume. These dimensions may be smaller depending on the layout of the PCB.

Interface Control Document | Revision - 1

### 3.2.3. Dimension of Monitor Subsystem

The size of the monitor subsystem at most will be around 5.5 x 17cm which is the size of a breadboard. This is to house the microcontroller and resistors that are needed for the input and outputs of the system. The size can be further decreased in the future if needed.

### 3.3. Mounting Locations

The entire system, excluding the wind turbine, shall be mounted on a sturdy wall inside the building supporting the wind turbine. The devices should be mounted in a location away from potential electrical hazards, and should accommodate enough wiring to and from the turbine so the wires do not have to be strained. All subsystems should be mounted in the same room so that maintenance may be readily performed.

Interface Control Document | Revision - 1

## 4. Thermal Interface

The charge controllers, utilizing power electronic circuits will require heatsinks to dissipate the heat generated by MOSFETs used in the circuits. Computer fans shall be mounted to aid in the cooling alongside the heatsinks.

Interface Control Document | Revision - 1

## 5. Electrical Interface

### 5.1. Primary Input Power

Input from the wind turbine will be 3-phase VAC.

### 5.2. Microcontroller Input Power

The microcontroller part of the monitor subsystem will be supplied with a separate battery supply with input up to 5V for the micro usb port and inputs between 7 and 12V for the VIN port.

### 5.3. Video Interfaces

The monitor subsystem will display information to a website hosted by the microcontroller that will be accessible to those on the same network.

### 5.4. User Control Interface

User interaction with the system will involve push buttons on the switch controller and monitor subsystems.

Interface Control Document | Revision - 1

## 6. Communications / Device Interface Protocols

### 6.1. Microcontroller Input and Output

The microcontroller we are using has a wide range of input and outputs. It consists of multiple ADC (Analog to Digital Converter) inputs that can be utilized to read signals from the battery with a voltage range of 0 to 3.3V. The microcontroller also has two DAC (Digital to Analog Converter) ports that can output up to 3.3V, which will be used to control the switch and charge controllers as needed.

### 6.2. Display/Website Monitor

The microcontroller will host a local website that will display the information on the battery status and power consumption and usage of the building. Users on the same network will be able to access this website.

Interface Control Document | Revision - 1

# Wind-Powered Building

# Reginald Sampson Maxwell Chen Colton Boos Peter Zha

# EXECUTION PLAN

Execution Plan | Revision - 2
| Jan 31 | Feb 7 | Feb 14 | Feb 21 | Feb 28 | Mar 7 | Mar 14 | Mar 21 | Mar 28 | Apr 4 | Apr 11 | Apr 18 | Apr 25 | Apr 30

ConOps Report
Research and Identify Parts

Conceptual Subsystem Designs

FSR, ICD, Execution and Validation Plans

Midterm Presentation
High Level Subsystem Designs

Simulate and Develop
Converter
Simulate and Develop
Inverter
Simulate and Develop Rectifier

Develop Battery Monitor
Calculate Power Usage and Generated

Develop theory for charge controller

Status Update Presentation

Develop Local Website for System Monitor

Finalize calculations for charge controller

Test switching for charge controller

Prepare Output Signal for Switch Controller

Develop Boost Converter

Final Presentation
Connect Rectifier and Converter

Final Demo
Final Report

Completed

In Progress

Behind Schedule

# Wind-Powered Building

# Reginald Sampson Maxwell Chen Colton Boos Peter Zha

# VALIDATION

Validation | Revision - 2
Subsystem | Validation Requirements | Status

Inversion and Conversion Subsystem

DC-AC Conversion | 12VDC is converted to 12VAC | Completed

Transformer Step-up

Transformer output is 120VAC given 12VAC
input | Completed
Inverter Output | Connected outlet outputs 120VAC | Completed
Converter with battery | Circuit elements function properly with battery voltage | Completed
Converter Output | Output meets DC voltage requirements of LEDs | Completed

Rectification and Conversion Subsystem

AC-DC Conversion | 2-15VAC is rectified to corresponding DC with < 0.2 V output ripple | Completed
DC-DC Conversion | 4-15VDC is converted to 15VDC | Completed
Connect Rectifier and Converter | Voltage output 15 VDC | Completed

Charge and Switch Controller Subsystem

Charge controller circuit validation | Conceptual circuit matches with parameters | Completed
Input/Output | Switch correctly transfers input power to output | Completed
Load Capacity | circuit can withstand expected load of input and
| output | Completed
Switch Validation | The switch correctly switches between outputs | Completed

Monitor Subsystem
Battery Capacity Monitor | System is able to successfully track the capacity of the battery | Completed

Display Power Generated and Power
Usage

System is able to display the power generated from the Wind Turbine, and the power used by the building

Completed

Website for System Monitoring

Website is accessible and cleanly displays
information about the entire system | Completed

Output Signal for Switch Controller

System will have triggers for specific cases of when
each battery should be used or charged.
Further implementation will be done in 404

Completed

I

# Wind-Powered Building

# Reginald Sampson Maxwell Chen Colton Boos Peter Zha

# SUBSYSTEM REPORTS

Subsystem Reports | Revision - 1

I

### SUBSYSTEM REPORTS

### FOR

## Wind-Powered Building

PREPARED BY:

_____________________________
Author | Date

APPROVED BY:

Colton Boos | 04/30/22
Project Leader | Date

_____________________________
John Lusher II, P.E. | Date

_____________________________
T/A | Date

Subsystem Reports | Revision - 1

II

### Change Record

Rev. | Date | Originator | Approvals | Description
Draft | 04/30/2022 | Colton Boos | | Draft Release

Subsystem Reports | Revision - 1

III

### Table of Contents

Table of Contents | III
List of Tables | IV
List of Figures | V

Subsystem Reports | Revision - 1

IV

### List of Tables

Table 4. Observation of Voltage Regulator Output Increasing with Input Voltage...... 11

Subsystem Reports | Revision - 1

V

### List of Figures

Subsystem Reports | Revision - 1

## 1. Introduction

The Wind-Powered Building project focuses on the power systems that convert, monitor, and store the power generated from a wind turbine to be delivered to an individual home. Each subsystem divides the overall system into relevant, manageable portions that each serve a different purpose. The rectifier and converter, the charge and switch controllers, the inverter and converter, and the monitor subsystems each manage a portion of the power delivery system. This system also features the use of two batteries for simultaneous charging and discharging, allowing for more efficient power gathering and delivery. Thorough validation testing was conducted on each subsystem to verify the working principles of each system in preparation for future system integration.

Subsystem Reports | Revision - 1

## 2. Rectification and Conversion Subsystem Report

### 2.1. Subsystem Introduction

The Rectification and Conversion Subsystem is designed to transfer the energy generated by the wind-turbine into a more usable form. This subsystem is crucial for charging the battery bank and was designed around those specifications. The wind-turbine will generate electricity when wind speeds are high enough, and this subsystem will be operating during those times.

### 2.2. Subsystem Details

The Rectification and Conversion Subsystem involves two circuits: a three-phase rectifier and a boost converter. These circuits are connected in series and were designed with that in mind. The goal of this subsystem is to charge the battery bank, however, the overall output passes through a separate subsystem prior to the bank.

### 2.2.0. Three-phase Rectifier Details

Figure 1. Rectification and Conversion Subsystem Block Diagram

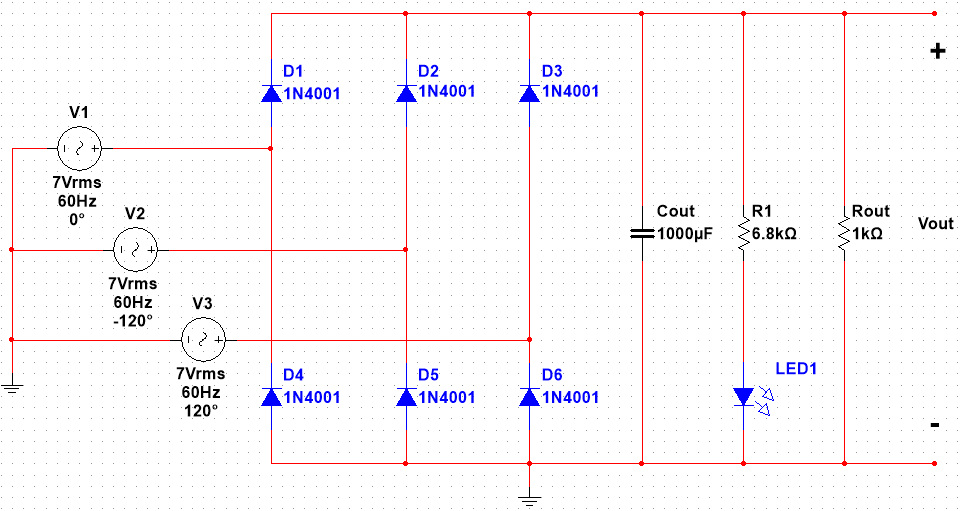
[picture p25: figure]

Figure 2. Schematic of Three-phase Rectifier

Subsystem Reports | Revision - 1

Considering the flow of power, from energy generation to electrical output, the three-phase rectifier is the first circuit in this path. It is directly connected to the wind-turbine and is
where the circuit receives its inputs. Three identical AC voltages make up this input, each one being 120 degrees out-of-phase with one another. Through a network of diodes, the circuit will rectify the input and achieve a DC output. The output power will fluctuate with respect to the wind speed, and a range of voltages will be passed onto the next circuit in this subsystem. There is an associated output voltage ripple with this rectifier, which was minimized with the use of a large enough capacitor.

### 2.2.1. Boost Converter Details

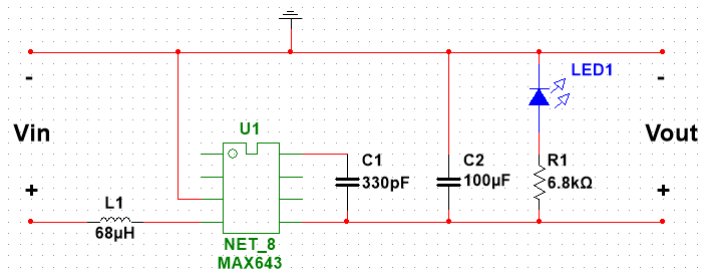
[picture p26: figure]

The goal of this boost converter is to take in a variety of input voltages then proceeds to output a constant voltage. Through experimentation, a boost topology was chosen since the wind-turbine will be generating voltages less than that of charging the battery. For the input, this circuit was designed around receiving a wide range of voltages from the rectifier. For the output, this circuit was also considered around specifications for charging the battery bank given by the manufacturer. The batteries will be charged using the constant voltage method and a range of 14.6V to 15V is specified. I elected to use the MAX643 voltage regulator which has an output voltage of 15V. The upper limit of charging the batteries were chosen by considering losses and voltage drops across the system. This regulator was also chosen for flexibility as it allows the use of a resistor divider and feedback pin to set the output voltage if it ever needs changing.

### 2.3. Subsystem Validation

This subsystem was thoroughly tested and validated according to criteria specified in Table 1 below. The three-phase rectifier was first designed and simulated in Multisim where it was then implemented on a breadboard and subjected to preliminary testing. After this, the circuit and all its components were soldered onto Perfboard, where final testing was applied.

For the boost converter, there was no simulation due to the absence of the MAX643 voltage regulator and its libraries on Multisim and other platforms. Starting from the implementation

Figure 3. Schematic of Boost Converter

Subsystem Reports | Revision - 1

on breadboard, it was verified to be working properly before moving on. After this, the circuit was soldered onto Perfboard. From here, a multitude of tests were performed, and the bulk of the data gathered lies in this aspect.

Test Name | Criteria | Methodology
Rectification with Output Voltage Ripple | Ripple < 0.2Vpp | Apply various input voltage amplitudes and measure Vpp of output voltage
DC-DC Conversion with Load | 15V output with ± 1% tolerance | Apply various input voltages and measure output voltage
Serial Test | 15V output with ± 1% tolerance | Connect rectifier and boost converter in series

### 2.3.0. Three-phase Rectifier Validation

Once the rectifier was simulated, the first test performed was measuring the output voltage ripple. After the final circuit was built on Perfboard, experimental data was gathered. Both tests are shown in the following Figure 4.

Voltage Ripple (mVpp); Input Voltage (Vp); Measuring Output Voltage Ripple; Simulation; Experimental; Extrapolated

Starting with the simulated data, a three-phase voltage source was varied from 0.5V to 15V in 0.5V increments; the voltage ripple was measured at the output. Experimental data was gathered using the Analog-Discovery 2, however, this machine has a maximum input voltage amplitude of 5V and can only support two waveform inputs. Due to this, the voltage ripple at the output will be affected and is the reason for the difference among the two cases. Using the extrapolated data from the experimental results, our validation criteria is still satisfied and shows that the circuit can perform under less-than-ideal circumstances.

Table 1. Validation Plan

Figure 4. Validation of Output Voltage Ripple

Subsystem Reports | Revision - 1

Moving on, we can use the same process above, but instead measure the rectified output voltage as seen in Figure 5. The simulated and experimental results match up very closely and the expectation is for that to continue. It is a linear relationship, therefore we can

Output Voltage (VDC); Input Voltage (Vp); Voltage; Simulation; Experimental

calculate the DC voltage given any input amplitude by VDC =

### 2.3.1. Boost Converter Validation

For the boost converter, all data presented in this section was gathered at the final stage when the circuit was on built on Perfboard.

The output of the boost converter was validated by a DC power supply and a DC load machine. The input was fed from the power supply by varying the voltage from 2V to 15V in 0.5V increments. The output was measured directly by the load machine while it drew a specific amount of current. By doing so, this is a good way to simulate the result of charging a battery. Eight different load currents were tested to see how the output voltage changed with respect to the input voltage. In total, as the load current increases, it requires a higher input voltage to supply a constant 15V. This is shown in Figure 6 below.

Another way to visualize this data is in Table 2 where we can more closely examine the output voltages that are desired. By focusing on the specified output of 15V with ± 1% tolerance, this corresponds to a range of acceptable voltages of 14.85V to 15.15V. Input voltages are given in the left column, while load currents are specified in the top row. Therefore, each entry in the Table 2 corresponds to a measured output voltage. The entries that satisfy our validation requirement are highlighted in green. There are a wide range of valid entries that show exactly how much input voltage we need to supply a certain load current.

Using the same methodology with the DC power supply and DC load machine, we can also see the effects of input current given in Figure 7. It takes a higher input current to supply an increasingly higher load current. Due to the IC overheating, any input current over 0.65A was cut off, which affected data collection for the load current of 400mA.

### Measuring Input Voltage Amplitude vs. Rectified Output

Figure 5. Relationship between Input Voltage Amplitude and Output Voltage

### Comparing the Effects of Different Load Currents on Output Voltage vs Input Voltage

Subsystem Reports; Revision - 1; Output Voltage (V); Input Voltage (V); Input Current (A)

Figure 6. Validation of Boost Converter with Load

Comparing the Effects of Different Load Currents on Input

Current vs Input Voltage

Figure 7. Effect of Input Current with Load

Subsystem Reports | Revision - 1

Load Currents (mA)
33 | 50 | 75 | 100 | 150 | 200 | 250 | 300 | 350 | 400
0.5 | 0 | 0 | 0 | 0 | 0 | 0 | 0 | 0 | 0 | 0
1 | 0 | 0 | 0 | 0 | 0 | 0 | 0 | 0 | 0 | 0
1.5 | 0 | 0 | 0 | 0 | 0 | 0 | 0 | 0 | 0 | 0
2 | 1.213 | 1.18 | 1.091 | 1.11 | 1.061 | 0.934 | 1.002 | 0.885 | 0.939 | 0.888
2.5 | 1.712 | 1.68 | 1.587 | 1.506 | 1.56 | 1.541 | 1.502 | 1.396 | 1.435 | 1.382
3 | 1.76 | 2.189 | 2.04 | 2.052 | 2.054 | 2.045 | 1.998 | 1.912 | 1.947 | 1.886
3.5 | 2.796 | 2.705 | 2.593 | 2.556 | 2.502 | 2.541 | 2.49 | 2.416 | 2.443 | 2.377
4 | 11.248 | 8.835 | 6.631 | 3.104 | 2.994 | 2.957 | 2.991 | 2.911 | 2.95 | 2.876
4.5 | 13.195 | 10.756 | 8.733 | 3.586 | 3.49 | 3.544 | 3.495 | 3.424 | 3.449 | 3.37
5 | 14.655 | 12.155 | 9.995 | 8.05 | 4.02 | 3.982 | 4.002 | 3.933 | 3.95 | 3.889
5.5 | 14.912 | 14.156 | 11.815 | 9.999 | 4.625 | 4.559 | 4.503 | 4.447 | 4.449 | 4.391
6 | 14.929 | 14.89 | 13.209 | 10.976 | 9.357 | 4.951 | 4.995 | 4.953 | 4.948 | 4.895
6.5 | 14.944 | 14.897 | 14.376 | 12.896 | 10.702 | 10.223 | 5.489 | 5.467 | 5.445 | 5.401
7 | 14.966 | 14.919 | 14.866 | 14.21 | 11.844 | 11.26 | 10.32 | 5.983 | 5.937 | 5.905
7.5 | 14.966 | 14.939 | 14.883 | 14.846 | 12.98 | 12.123 | 11.512 | 6.531 | 6.49 | 6.455
8 | 14.988 | 14.976 | 14.89 | 14.853 | 14.083 | 13.1 | 12.539 | 7.006 | 6.94 | 6.922
8.5 | 15.007 | 14.995 | 14.922 | 14.866 | 14.848 | 13.98 | 13.503 | 7.53 | 7.436 | 7.439
9 | 15.025 | 15.01 | 14.966 | 14.912 | 14.836 | 14.8 | 14.433 | 8.05 | 7.96 | -
9.5 | 15.042 | 15.03 | 15.01 | 14.939 | 14.893 | 14.804 | 14.753 | 14.74 | 8.466 | -
10 | 15.06 | 15.047 | 15.037 | 15 | 14.961 | 14.866 | 14.765 | 14.672 | 8.985 | -
10.5 | 15.056 | 15.049 | 15.044 | 15.039 | 14.978 | 14.937 | 14.875 | 14.77 | 9.518 | -
11 | 15.074 | 15.066 | 15.064 | 15.064 | 14.993 | 15.017 | 14.939 | 14.848 | 14.724 | -
11.5 | 15.096 | 15.088 | 15.083 | 15.083 | 15.059 | 15.074 | 14.998 | 14.939 | 14.851 | -
12 | 15.115 | 15.11 | 15.108 | 15.105 | 15.098 | 15.115 | 15.091 | 15.02 | 14.88 | -
12.5 | 15.16 | 15.147 | 15.142 | 15.142 | 15.135 | 15.122 | 15.16 | 15.056 | 15.078 | -
13 | 15.186 | 15.174 | 15.174 | 15.176 | 15.174 | 15.164 | 15.23 | 15.181 | 15.12 | 14.88
13.5 | 15.235 | 15.223 | 15.22 | 15.218 | 15.215 | 15.213 | 15.284 | 15.262 | 15.191 | 15.152
14 | 15.286 | 15.274 | 15.259 | 15.272 | 15.277 | 15.269 | 15.357 | 15.338 | 15.291 | 15.218
14.5 | 15.345 | 15.335 | 15.33 | 15.343 | 15.345 | 15.34 | 15.431 | 15.409 | 15.374 | 15.284
15 | 15.453 | 15.46 | 15.423 | 15.46 | 15.458 | 15.546 | 15.521 | 15.489 | 15.418 | 15.328

Input Voltage (V)

Table 2. Validation of Boost Converter Output Voltage with Tolerances

Subsystem Reports | Revision - 1

### 2.3.2. Serial Connection Validation

With the rectifier and boost converter connected in series, we can test the output voltage of the subsystem. Again, using the Analog-Discovery 2, we can apply two input waveforms to the rectifier while measuring output voltage of the boost converter. Once an input voltage amplitude of 1.8V is applied, the boost converter is activated and starts outputting 15V. This 15V is carried all the way up to the maximum input amplitude of 5V. It is also well within the ± 1% tolerance once the boost converter turns on. Higher input voltage amplitudes will continue to produce 15V at the output of the boost converter, but such tests cannot be performed with the limitations of the Analog-Discovery 2.

Output Voltage (V); Input Voltage Amplitude (Vp; Serial Connection Test

### 2.4. Subsystem Conclusion

Each of the circuits built were shown to have worked and are verified against the validation criteria. With the rectifier, I’ve shown that there is minimal output voltage ripple and less than the 200mVpp requirement along with the linear relationship between input voltage amplitude and rectified output voltage. For the boost converter, I’ve compared the effects of eight increasing load currents while measuring output voltage and input current. There are multiple options that satisfy the output voltage of 15V ± 1%. By electing to charge the batteries with a specific amount of current, we know exactly how much input power is needed. Finally, when both circuits are connected in series, it is shown that the validation requirement is met again.

Figure 8. Validation of Serial Connection

Subsystem Reports | Revision - 1

## 3. Charge and Switch Controller Subsystem Report

### 3.1. Subsystem Introduction

The charge and switch controller subsystem is designed to divert power to and from the batteries to prevent overcharge and output control. The overall power system will be unique in that there will be two batteries in use simultaneously, so the working principle of a typical charge controller system will require slight modification. The charge controller subsystem is focused on switching between the two batteries in order to prevent over charging of each. The second switch determines which battery to draw the output power from. The overall system allows one battery to charge and the other to discharge simultaneously, making the overall power system more efficient than a one battery system. Eventually the charge and switch controller system will be combined with the Monitor Subsystem, which will control the switches based on a signal output from a microcontroller. “After deliberation with the sponsor, the switch controller will simply be achieved through gate-driven logic”

### 3.2. Subsystem Validation

The charge controller will make up the bulk of the implementation for this subsystem, and as such warranted the most research. A circuit borrowed from an online resource was used for the implementation because its design closely matched the specifications required for charging the batteries purchased. This circuit is based on self-regulated switching, which means it does not rely on an external signal to drive the switch. The key components of the circuit are the 12V SPDT (single pole double throw) relay and TL7808 operational amplifiers. The operating principle for the circuit is the use of the operational amplifiers as comparator switches. The default connection for the combination relay will divert incoming power from the wind turbine to the battery. This voltage will also be fed into the first two amplifiers, which have two comparator configurations: the first has a reference voltage set high, so that when the input voltage exceeds it the resulting output should trigger the relay and divert to the dump load. Practically, this means that the battery is fully charged, so according to the battery specifications, this high reference voltage will be at 15V. The second comparator will have a reference voltage set low, so that when the input voltage drops below it, the relay will switch off, diverting the current flow back to the batteries. In accordance with battery specifications, the low reference voltage will be around 10.5V.

Subsystem Reports | Revision - 1


The primary goal of validation for the charge controller is to confirm that the relay will properly switch when the input voltage exceeds the high reference voltage and drops below the low reference voltage, and the voltage of the comparator output is used to confirm this operation. For validation, a couple of changes were made to the borrowed circuit. Firstly, the dump load was to be replaced with the second battery, as the operation between two batteries was more important than the presence of the dump load. Secondly, the potentiometers used to adjust the reference voltages were changed from 10k to 100k in order to allow greater variability on the reference voltages values.

Switching was eventually accomplished but at a low voltage setting with 5V input due to the low-current limitations of the breadboard the circuit was built on. The low reference was set to 2.00V while the high reference was set to about 0.4V, so as Vin exceeds 2.00V, the output on the comparator affecting the relay, Opamp3, should be high.

Vin (V) | Opamp2 Out (V) | Opamp1 out (V) | Opamp3 out (V) | Opamp4 -in (V)
1.5 | 2.68 | 2.64 | 0.59 | 2.02
3.3 | 0.042 | 2.47 | 2.37 | 1.92

However, several issues arose that required changes before this conclusion could be reached. Firstly, the relay did not switch with changing input voltage, and it was soon discovered that the voltage regulator output increased directly with the input voltage.

Figure 9. Schematic for Charge Controller

Table 3. Comparator Voltage Measurements Confirm Successful Switching Behavior

Subsystem Reports | Revision - 1
Vin (V) | VregOut (V) | Comparator Vin (V)
5 | 4.078 | 1.08
6 | 4.945 | 1.32
7 | 5.854 | 1.56
8 | 6.778 | 1.81
9 | 7.711 | 2.05
10 | 8.646 | 2.27
10.5 | 9.109 | 2.38
11 | 9.582 | 2.5
11.5 | 10.054 | 2.65
12 | 10.523 | 2.77
12.5 | 10.993 | 2.89
13 | 11.465 | 3.02
13.5 | 11.936 | 3.13

This was unexpected behavior as the voltage regulator used was rated at 8V, so the output should not have exceeded 8V. The regulator was swapped a couple times, but the problem persisted. This in turn affected both low and high reference voltages, since they were directly related to the regulator output. This essentially locks the ratio between input voltage and reference voltage, and the only way to modify the output of the comparators was to adjust the reference voltages.

The issue with the input voltage was also an opportunity. The input voltage to be compared against the reference voltages was removed from the input and replaced with an external voltage source. This modification much more closely matched the intended goal of switch control being driven by an external signal provided by the Monitor Subsystem.

A second issue regarding the reference voltages also hindered the expected functionality of the circuit. The high reference voltage apparently had no effect on the relay switch, and by solely adjusting the low reference voltage the relay was able to switch on and off. Each combination of high and low was tested with a test voltage of 7V, and a fixed comparator input voltage of 1.04V. Here VrefLow represents the low reference voltage while VrefHigh represents the high reference voltage.

Table 4. Observation of Voltage Regulator Output Increasing with Input Voltage

Subsystem Reports | Revision - 1
VrefLow (V) | VrefLow > VrefHigh | Opamp2 out (V) | Opamp1 out (V) | Opamp3 out (V) | Opamp4 -in (V)
3.38 adjust to 0.99 | Vin > VrefLow(only) | N/A | N/A | N/A | N/A
VrefHigh (V) | Vin > VrefHigh(only) | 2.724 | 2.657 | 0.63 | 2.04
0.45 | Vin > both | 0.011 | 2.504 | 2.407 | 1.93
VrefLow (V) | VrefLow < VrefHigh | Opamp2 out (V) | Opamp1 out (V) | Opamp3 out (V) | Opamp4 -in (V)
0.411 | Vin > VrefLow(only) | 0.023 | 0.014 | 2.405 | 1.934
VrefHigh (V) | Vin > VrefHigh(only) | N/A | N/A | N/A | N/A
3.21 adjust 0.928 | Vin > both | 0.018 | 2.503 | 2.385 | 1.926

Using logic analysis, the only time the output of amplifier 3, and therefore the relay, is affected is when VrefLow drops below the comparator input voltage. There appears to be no effect on the output whether VrefLow is greater or less than VrefHigh, or whether VrefHigh is greater than the comparator input voltage. Interestingly, at higher input voltages such as 12 V, the comparator output operates closer to its expected behavior, and adjusting both the value of VrefHigh and VrefLow appears to control the output; a low VrefLow and high VrefHigh yields a high output, and a low VrefHigh yields a low output. However, this behavior was not consistent, and subsequent tests did not yield the same results.

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
0 | 1 | 2 | 3 | 4 | 5 | 6

Opamp3 Out (V)

VrefLow (V)

### Comparator Out vs VrefLow (VrefHigh = High)

Table 5. Thorough Comparison of VrefLow and VrefHigh Behavior

Figure 10. VrefLow Effect on Output with VrefHigh Set High

Subsystem Reports | Revision - 1

### 3.3. Subsystem Conclusion

Initially the expected behavior of the circuit did not operate correctly, and thus necessary changes were made in order to better operate its behavior. The modifications to the reference voltages and switching signal input were simple but effective solutions to operate the circuit as intended. Validation tests confirmed successful switching of the relay and correct output behavior of the amplifiers. Though results appeared different at higher input voltages, the behavior was mostly inconsistent and firm conclusions could not be drawn. After reviewing the demonstration, the professor’s advice was to swap out comparators and relays for transistor-based switching for more proper integration with the other subsystems.

0

0.2

0.4

0.6

0.8

1

0 | 1 | 2 | 3 | 4 | 5 | 6

Opamp3 Out (V)

VrefLow (V)

## Comparator Out vs VrefLow (VrefHigh = Low)

Figure 11. VrefLow Effect on Output with VrefHigh Set Low

Subsystem Reports | Revision - 1

## 4. Monitor Subsystem Report

### 4.1. Subsystem Introduction

The Monitor Subsystem is designed to monitor the battery life of the Wind-Powered Building providing valuable information to the user through a website the user will be able to access on the network. In addition, this subsystem will also be in charge of controlling the Charge and Switch Controller Subsystem sending a signal to control which battery will be charged by the wind turbine and which battery will be used to power the building.

### 4.2. Subsystem Details

The Monitory Subsystem utilizes an ESP32 microcontroller to read in inputs from a power a source. This microcontroller is equipped with multiple ADC (Analog to Digital Converter) ports allowing it take in inputs from the two batteries that are in our system. It also comes equipped with two DAC (Digital to Analog Converter) ports which is a sufficient amount to output a signal to the Charge and Switch Controller Subsystem. Finally, the microcontroller is equipped with Wi-Fi and Bluetooth capabilities which will be used to host a local website for the user to access.

The ADC ports on the microcontroller are only able to take in voltages between 0 and 3.3V. Because of this voltage dividers must be utilized to step down the voltage from our battery which can range from 10 up to 14V. Furthermore, the ADC ports have trouble detecting voltage differences at very low and very high voltages, however this should not be an issue since to optimally charge the battery we do not want to charge the battery when it is almost dead or likewise keep charging it when it is almost full. The DAC ports can only output voltages between 0 and 3.3V, which will be a restriction on the design of the Charge and Switch Controller Subsystem. Using the information received from the ADC ports the microcontroller will output a signal using the DAC ports to the Charge and Switch Controller Subsystem telling it which battery to charge and which battery to use. This is something that will be worked on more later as it involves integration of subsystems, however preparations have been made to allow for easy integration.

Utilizing the Wi-Fi and Bluetooth capabilities a local website will be hosted by the microcontroller. This website will display information on the statuses of the two batteries as well as other information such as the power usage and generated by the Wind-Powered Building. A user on the same network can access this website through the IP-Address of the microcontroller.

A PCB will be added at a later date to replace the breadboard that currently houses all the components of the subsystem.

### 4.3. Subsystem Validation

Validation for the battery monitor portion was done by inputting various voltage levels into the microcontroller. Using a power supply various voltage levels were tested on the microcontroller. Print statements outputting to a console were written in the code to see if the microcontroller was reading the voltage levels properly. First lower voltages were tested to see if the microcontroller was reading properly. Afterward higher voltage levels up to 14V were tested to see if the voltage divider was function as intended.

Subsystem Reports | Revision - 1

In preparation for integration with the Charge and Switch Controller Subsystem code was written that will trigger print statements to the console when either battery reaches a certain threshold. These print statements will later be replaced to instead send a signal to the Charge and Switch Controller Subsystem. The figure below shows the print statements outputted to the console during testing.

The flow chart in Figure 13 shows the logic used when determining which battery should be charged and used


Validation for the website was done by yet again using a power supply
to test various voltage levels on the microcontroller. The website was then checked to see if the correct information was displayed. Furthermore, while testing various voltages the website was also checked to ensure that the values were updating properly. On the side in figure X is a picture of the current website on a mobile device displaying information to the user.

### 4.4. Subsystem Conclusion

Currently the Monitor Subsystem is functioning properly, being able to track level of both batteries and displaying that information onto the website. Some aspects will need to be further tested once integration begins with outputting voltage to the Charge and Switch Controller Subsystem. Finally further improvements can be made to the website UI for a cleaner and more user friendly look.

Figure 12. Console Output

Figure 14. Mobile Website

Figure 13. Flow Chart of Battery Management

Subsystem Reports | Revision - 1

## 5. Inversion and Conversion Subsystem Report

### 5.1. Subsystem Introduction

The inversion and conversion subsystem is designed to supply power to the building, to both a DC and AC load. The subsystem is powered by a battery which stores the wind power generated by the wind turbine. The inverter and converter were tested to validate their capability to power the building’s loads.

For both the inverter and converter circuits, I do not have working simulations or schematics due to no database having a CD4047 or LM2577 model in their library. I am working to find a program that allows me to design both because it is necessary to optimize andimplemt the circuits further.


### 5.1.0. Inverter without Transformer and Load

5.1.0.1. Operation
For the inverter, a CD4047 low power inverter is used in astable multivibrator configuration. The inverter outputs two alternating square waves to drive the IRFZ44 MOSFETs, so that only one is on at a given time. By repeatedly driving one MOSFET while the other is off, current is pushed and pulled through the windings of the transformer’s secondary side. Ideally supplying the transformer’s secondary winding with 24VAC (-12-0-+12) at around 60 Hz.
5.1.0.2. Validation
Test | Criteria | Methodology

Figure 15. Block Diagram of Inversion and Conversion Subsystem

Subsystem Reports | Revision - 1
Inverter without transformer or load | 24VAC output with 1% tolerance | Apply input voltages ranging from 10.5-14.7V and measure the output voltages at the MOSFETS drain
Inverter with transformer or load | 117VAC output with 1% tolerance | Apply input voltages ranging from 10.5-14.7V and measure the output voltages at the transformer’s primary terminal
Light Bulb Test | Light bulb turns on | Apply input voltages ranging from 10.5-14.7V and check if the light bulb turns on

To validate the inverter circuit, the circuit was first tested without the transformer or LED light bulb connected to the output. The output voltage of the inverter circuit was measured at the gate of both IRFZ44 MOSFETs with the positive end of the voltmeter probe connected to the drain and the negative end of the probe connected to the supply voltage (V+) of the inverter circuit. The input voltages that the output voltage was measured for ranged from 10.5-14.7V. The output voltage was measured over this specific range because the discharge voltage of the battery supplied to the converter has a minimum of 10.5V and maximum of 14.6V. The measured output voltages of the inverter circuit without the transformer and LED light bulb are displayed in Figure 16. The inverter was validated that it could produce 12VAC at its output when supplied with input voltages closer to the upper bound of the input voltage range. However, as the input voltages decreased the output voltage also decreased.


Input Voltage (VDC) | Current Draw (A)
10.5 | 0.992
10.8 | 0.991

Table 6. Inverter without Transformer and Load Validation Plan

Figure 16. Inverter without Transformer or Load Measured Output Voltage

Subsystem Reports | Revision - 1
11.1 | 0.991
11.4 | 0.991
11.7 | 0.991
12 | 0.99
12.3 | 0.99
12.6 | 0.989
12.9 | 0.989
13.2 | 0.988
13.5 | 0.988
13.8 | 0.988
14.1 | 0.988
14.4 | 0.987
14.7 | 0.987

To complete validation for the inverter circuit when the transformer and LED light bulb are disconnected, an oscilloscope was used to measure the waveform output at the drain of both IRFZ44 MOSFETs. In Figure 17 and Figure 18, the waveform is shown along with the frequency and peak to peak voltage. With both MOSFETs outputting a voltage ranging from 12.7-12.9VAC at a frequency of 60 Hz, the criteria needed to validate the output of the inverter circuit was confirmed.

Table 7. Current Draw of Inverter without Transformer or Load


Figure 17. First IRFZ44 Output Voltage and Frequency

Subsystem Reports | Revision - 1


### 5.1.1. Inverter with Transformer and Load

5.1.1.1. Operation
For the transformer, a 24VAC to 117VAC center tapped step-up transformer was used. Each of the transformer’s two 12V terminals are connected to drain (output) of the IRFZ44 MOSFET’s individually. The transformer’s 0V terminal on the secondary side is connected to the supply voltage (V+). On the primary side of the transformer, a 510VAC varistor is placed between the 117V and 0V terminals to reduce voltage spikes. Additionally, a 60W LED light bulb is connected to the transformer’s primary side 117V and 0V terminals. The function of the transformer is to step-up the inverter’s 24VAC output to about 117VAC at 60Hz, supplying power to the LED light bulb.
5.1.1.2. Validation
Test | Criteria | Methodology
Inverter with transformer or load | 117VAC output with 1% tolerance | Apply input voltages ranging from 10.5-14.7V and measure the output voltages at the transformer’s primary terminal
Light Bulb Test | Light bulb turns on | Apply input voltages ranging from 10.5-14.7V and check if the light bulb turns on

Since validation for the output of the inverter circuit was already completed the final steps for validation were to connect the output of the inverter to the secondary terminals of the transformer and then connect the primary terminals of the transformer to the LED light bulb. After these were connected testing of the AC output voltage was conducted by using a digital multimeter to measure the 117VAC and 0VAC terminals of the transformer using

Figure 18. Second IRFZ44 Output Voltage and Frequency

Table 8. Inverter with Transformer and Load Validation Plan

Subsystem Reports | Revision - 1

clamp cables. In addition, the LED light bulb was tested at the same time to check that it worked when supplied by the transformer output.

Input Voltage (VDC) | Inverter Output (VAC) | Transformer Output (VAC)
10.5 | 9 | 90.16
12 | 10.05 | 102.75
14.7 | 11.9 | 125.92

As shown in Table 9, because of safety concerns I measured the transformer’s output voltage at the upper and lower input voltage bounds and the ideal 12V input voltage. The data confirmed that the inverter connected with the transformer and LED light bulb met the validation criteria, but at the upper input bound as mentioned previously.

Input Voltage (VDC) | Inverter Output (VAC) | Transformer Output (VAC) | Light Bulb
14.7 | 11.9 | 125.92 | On
14.4 | 11.7 | 113.34 | On
14.1 | 11.49 | 103~112 | On
13.8 | 11.28 | 103~112 | Off

In Figure 19, a picture displaying the LED light bulb lighting up when supplied by the transformers output. This validates that the inverter passed the validation test checking that the LED light bulb turned on. Additionally, the transformers output voltages that could power the LED light bulb are shown in Table 10, providing us with the ideal input voltage range of 14.7-14.1VDC needed by the inverter to turn on the light bulb.

Table 9. Transformer Output at Boundary Input Voltages

Table 10. Input Voltage Range for Powering Light Bulb Load

Subsystem Reports | Revision - 1


### 5.2. Converter

### 5.2.1.5.2.0. Operation

For the Converter, a LM2577-ADJ step-up regulator IC is used. The function of the converter is to output a voltage ranging from 12 to 24VDC when supplied an input voltage ranging from 10.5 - 14.7V. A 100K variable resistor is implemented to allow for the output voltage to be adjusted.

### 5.2.2.5.2.1. Validation

Test | Criteria | Methodology
Converter without load (output lower bound) | 12VDC output with 1% tolerance | Apply input voltages ranging from 10.5-14.7V and adjust variable resistor for desired 12VDC output and measure the output voltages
Converter without load (output upper bound) | 24VDC output with 1% tolerance | Apply input voltages ranging from 10.5-14.7V and adjust variable resistor for desired 12VDC output and measure the output voltages
Converter with load | 12VDC output with 1% tolerance when LEDs are connected | Apply input voltages ranging from 10.5-14.7V and adjust variable resistor for desired 12VDC output when load is connected and measure the output voltages
LED lights Test | Dual LEDs turn on | Apply input voltages ranging from 10.5-14.7V and check if the LEDs turn on

Figure 19. Picture of Inverter Powering LED Light Bulb Successfully

Subsystem Reports | Revision - 1

The validation of the converter began by first measuring the output voltage of the converter without a load connected. The variable resistor of the circuit was adjusted to achieve an output of 12VDC. Then for 15 different input voltages ranging from 10.5 to 14.7V the output voltage was measured. The output voltage was measured over this specific range because the discharge voltage of the battery supplied to the converter has a minimum of 10.5V and maximum of 14.6V. However, no conclusive data was accurately collected for input voltages 10.5V and 13.2 - 14.7V because the output voltage was unstable and caused the LM2577 to overheat.


Similarly, to the first test, the variable resistor of the circuit was adjusted again to achieve an output of 24VDC. Likewise, the output voltage was measured again for the same input voltages used in the first no-load validation test. The output voltages were within 1% tolerance of the desired 24VDC. These tests validated demonstrate that the converter is capable of operating with no-load with input voltages ranging from 10.5-14.7V to output voltages ranging from 12-25V.

Table 11. Converter Validation Plan

Figure 20. No-load Output Voltages when 12V Desired


Subsystem Reports | Revision - 1

To validate the operation of the converter with the LEDs connected, the same input voltages ranging from 10.5 to 14.7V were supplied and the output voltage was measured. During testing the LED switch was turned on. A picture taken during one of the test trials is provided in Figure 22, to show that the LEDs produced light when supplied with 12VDC from the converter output. However, for input voltages between 10.5 - 10.8V, the output voltage was unstable and caused the LM2577 to overheat.

Figure 21. No-load Output Voltages when 24V Desired

Figure 22. Output Voltages when 12V Desired with Load Connected

Subsystem Reports | Revision - 1


### 5.3. Subsystem Conclusion

Both the inverter and converter circuits of the subsystem were demonstrated to operate properly, meeting the validation criteria. The inverter was able to receive input voltages of the expected range and supply power to the LED light bulb, displaying its ability to power the building’s AC load. Likewise, the converter was able to receive input voltages of the expected range and supply power to the dual LEDs, exhibiting its ability to power the building’s DC load. The behavior and results of the circuits differed from what was expected but improvements will be made by completing full simulations and implementing them on perfboards.

Figure 23. Picture of Converter Powering Dual LEDs successfully

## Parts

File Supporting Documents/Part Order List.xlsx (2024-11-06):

Order Date | Item | Part Number | Part Buy Link | Price Per Part | Quantity | Total | Item Description
3/3/2022 | ESP32 Microcontroller |  | https://www.amazon.com/HiLetgo-ESP-WROOM-32-Development-Microcontroller-Integrated/dp/B0718T232Z | $10.99 | 1 | $10.99 | MicroController for Monitor subsystem
3/3/2022 | 12V, 7.2 Ah Battery |  | https://www.amazon.com/Mighty-Max-Battery-Verizon-PX12072-HG/dp/B00OZMW232 | $19.99 | 2 | $39.98 | Main Energy Storage for whole project
3/3/2022 | Dyna-Living Wind Turbine Generator |  | https://www.amazon.com/Dyna-Living-Windgenerator-Controller-Automatic-Adjustment/dp/B08G4XRLCP | $184.99 | 1 | $184.99 | Wind turbine to generate power
 |  |  |  |  | Order Total | $235.96
 |  |  | Turbine after purchase (includes credit/debit card fees) | $195.88
 |  |  |  |  | Spent to Date | $246.85
2022-03-10 | Switching Regulator | LM2585T-ADJ/NOPB | https://www.digikey.com/en/products/detail/texas-instruments/LM2585T-ADJ-NOPB/308003 | $8.76 | 1 | $8.76 | IC to control the switching aspect of the boost converter
 |  |  |  |  | Order Total | $8.76
 |  |  |  |  | Spent to Date | $255.61
2022-03-24 | schottky diode | 1N5818G | https://www.digikey.com/en/products/detail/onsemi/1N5818G/1474209 | $0.45 | 4 | $1.80 | For use in the boost converter
 | 68uH Inductor | HCTI-68-7.7 | https://www.digikey.com/en/products/detail/signal-transformer/HCTI-68-7-7/7362978 | $3.02 | 2 | $6.04 | For use in the boost converter
 | 100uF Capacitor | 107KXM025M | https://www.digikey.com/en/products/detail/illinois-capacitor/107KXM025M/5410757 | $0.37 | 2 | $0.74 | For use in rectifier and boost converter
 | 470uF Capacitor | 25ZLH470MEFC10X12.5 | https://www.digikey.com/en/products/detail/rubycon/25ZLH470MEFC10X12-5/3563614 | $0.49 | 2 | $0.98 | For use in boost converter
 | Center Tapped Transformer (117VAC -> 24VAC, 3A) | 67-1243 | Center Tapped Transformer (117VAC -> 24VAC, 3A): Amazon.com: Industrial & Scientific (https://www.amazon.com/Center-Tapped-Transformer-117VAC-24VAC/dp/B00SOXR16Q) | $24.95 | 1 | $24.95 | Center Tapped Transformer Used for power supplies, rectifier, or filter circuits
 | NE555 IC | 296-NE555P-ND | NE555P Texas Instruments | Integrated Circuits (ICs) | DigiKey (https://www.digikey.com/en/products/detail/texas-instruments/NE555P/277057) | $0.40 | 2 | $0.80 | 555 Type, Timer/Oscillator (Single) IC 100kHz 8-PDIP
 | IRF540 Mosfet | IRF540ZPBF-ND | IRF540ZPBF Infineon Technologies | Discrete Semiconductor Products | DigiKey (https://www.digikey.com/en/products/detail/infineon-technologies/IRF540ZPBF/666094) | $1.34 | 3 | $4.02 | N-Channel 100 V 36A (Tc) 92W (Tc) Through Hole TO-220AB
 | BA159 Diode | BA159G A0G | BA159G A0G Taiwan Semiconductor Corporation | Discrete Semiconductor Products | DigiKey (https://www.digikey.com/en/products/detail/taiwan-semiconductor-corporation/BA159G-A0G/7357159) | $0.50 | 3 | $1.50 | Diode Standard 1000 V 1A Through Hole DO-204AL (DO-41)
 | 12V Zener Diode | 1N963BMS-ND | 1N963B Microchip Technology | Discrete Semiconductor Products | DigiKey (https://www.digikey.com/en/products/detail/microchip-technology/1N963B/4377365) | $2.31 | 3 | $6.93 | Zener Diode 12 V 500 mW ±5% Through Hole DO-7
 | 40uH Inductor | HM3335-ND | 1537H Hammond Manufacturing | Inductors, Coils, Chokes | DigiKey (https://www.digikey.com/en/products/detail/hammond-manufacturing/1537H/454736) | $6.41 | 1 | $6.41 | 40 µH Unshielded Molded Inductor 5 A 39mOhm Axial
 | 50k Potentiometer | 2197-313-2441F-50K-ND | 313-2441F-50K Xicon | Potentiometers, Variable Resistors | DigiKey Marketplace (https://www.digikey.com/en/products/detail/xicon/313-2441F-50K/10487969) | $2.95 | 1 | $2.95 | 50k Ohm 1 Gang Linear Panel Mount Potentiometer - 1.0 Kierros - - Solder Lug
 | IRFZ44 Mosfet | IRFZ44VZPBF-ND | IRFZ44VZPBF Infineon Technologies | Discrete Semiconductor Products | DigiKey (https://www.digikey.com/en/products/detail/infineon-technologies/IRFZ44VZPBF/666098) | $1.94 | 3 | $5.82 | N-Channel 60 V 57A (Tc) 92W (Tc) Through Hole TO-220AB
 | IRF4905 | IRF4905PBF-ND | IRF4905PBF Infineon Technologies | Discrete Semiconductor Products | DigiKey (https://www.digikey.com/en/products/detail/infineon-technologies/IRF4905PBF/812139) | $2.43 | 1 | $2.43 | P-Channel 55 V 74A (Tc) 200W (Tc) Through Hole TO-220AB
 | 1N4001 | 1N4001GP-E3/54 | 1N4001GP-E3/54 Vishay General Semiconductor - Diodes Division | Discrete Semiconductor Products | DigiKey (https://www.digikey.com/en/products/detail/vishay-general-semiconductor-diodes-division/1N4001GP-E3-54/2142384) | $0.52 | 2 | $1.04 | Diode Standard 50 V 1A Through Hole DO-204AL (DO-41)
 | 100uH Inductor | 399-20012-ND | SBCP-47HY101B KEMET | Inductors, Coils, Chokes | DigiKey (https://www.digikey.com/en/products/detail/kemet/SBCP-47HY101B/9842513) | $1.15 | 1 | $1.15 | 100 µH Unshielded Wirewound Inductor 500 mA 584mOhm Max Radial, Vertical Cylinder (Open)
 |  |  |  |  | Order Total | $67.56
 |  |  |  |  | Spent to Date | $323.17
2022-09-05 | Hi LetGo Voltage Sensor |  | https://www.amazon.com/HiLetgo-Voltage-Detection-Arduino-Electronic/dp/B01HTC4XKY | $5.49 | 1 | $5.49 | Voltage Sensor for the monitoring sub system
 | INA219 Hi LetGo Current Sensor |  | https://www.amazon.com/HiLetgo-INA219-Bi-Directional-Current-Breakout/dp/B07VL8NY32?s=industrial | $8.99 | 1 | $8.99 | Current sensor for monitoring sub system
 | Power MOSFET | STP36NF06L | https://www.amazon.com/Todiys-STP36NF06L-N-Channel-Transistor-STP36NF06/dp/B088ND1ZNQ | $7.98 | 1 | $7.98 | 60V 30A Power MOSFET for switching and passing current and voltage
 |  |  |  |  | Order Total | $22.46
 |  |  |  |  | Spent to Date | $345.63
2022-09-08 | LTC3780 | LTC3780IG#PBF | https://www.mouser.com/ProductDetail/584-LTC3780IG%23PBF | $14.29 | 2 | $28.58 | Switching regulator IC for boost converter
 | 1000uF Capacitor | EEU-FR1V102 | https://www.mouser.com/ProductDetail/667-EEU-FR1V102 | $1.44 | 4 | $5.76 | output capacitor for rectifier
 | Rectifier Diode | 1N5401RLG | https://www.mouser.com/ProductDetail/863-1N5401RLG | $0.39 | 10 | $3.92 | diode for rectifier
 | Fuse | 0251012.NAT1L | https://www.mouser.com/ProductDetail/576-0251012.NAT1L | $1.57 | 3 | $4.71 | Fuse for rectifier
 | Sense resistor | WLAR020FE | https://www.mouser.com/ProductDetail/588-WLAR020FE | $1.77 | 3 | $5.31 | sense resistor for boost converter
 | MOSFETs | IRF530PBF-BE3 | https://www.mouser.com/ProductDetail/78-IRF530PBF-BE3 | $1.30 | 7 | $9.10 | Transistor for boost converter
 | Schottky Diode | MBR745G | https://www.mouser.com/ProductDetail/863-MBR745G | $0.94 | 10 | $9.42 | Diodes for boost converter
 |  |  |  |  | Order Total | $66.80
 |  |  |  |  | Spent to Date | $412.43
2022-09-18 | P-channel Power MOSFET | IRF9540N | https://www.amazon.com/dp/B0854HJ43H/?coliid=I1NT8FJ0SFYV5L&colid=8DOP4CG5NFPQ | $8.99 | 1 | $8.99 | p-channel MOSFETs for high-side load switching
 | 4.7uH inductor | 2000-4R7-H-RC | https://www.mouser.com/ProductDetail/Bourns/2000-4R7-H-RC?qs=lSaKIV153ii30Wc3juSlOQ%3D%3D | $2.60 | 2 | $5.20 | Inductor for boost converter
 | analog potentiometer | 3296Y-1-103LF | https://www.mouser.com/ProductDetail/652-3296Y-1-103LF | $2.43 | 2 | $4.86 | to control output voltage of boost converter
 | AA battery holder | 2462 | https://www.digikey.com/en/products/detail/keystone-electronics/2462/303811 | $1.29 | 2 | $2.58 | To supply 3V to enable pin on boost converter IC
 |  |  |  |  | Order Total | $21.63
 |  |  |  |  | Spent to Date | $434.06
2022-10-17 | wind speed measurement device | Hallocool handheld anemometer device | https://www.amazon.com/dp/B09K7WD5CK?s=industrial&sp_csd=d2lkZ2V0TmFtZT1zcF9kZXRhaWw | $15.99 | 1 | $15.99 | For measuring wind speeds, will tell us what wind speeds we can charge the batteries at and other important information
 |  |  |  |  | Order Total | $15.99
 |  |  |  |  | Spent to Date | $450.05

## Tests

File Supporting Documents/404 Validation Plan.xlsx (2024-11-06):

Responsible Engineer(s) | Test Name | Validation Requirements | Methodology | Status
Reggie | DC-AC Conversion Test | 12VDC is converted to 12VAC | Input DC voltage to the inverter and measure the output AC voltage before the transformer (with the transformer disconnected) | Completed
Reggie | Transformer Step-up Test | Transformer output is 120VAC given 24VAC input | Input DC voltage to the inverter and measure the output AC voltage of the transformer using a digital multimeter | Completed
Reggie | Inverter Output Test | Connected outlet outputs 120VAC and powers a load | Input DC voltage to the inverter and measure the output AC voltage of the transformer using a digital multimeter and plug in an iphone charger to the outlet | Completed
Reggie | Converter with battery | Circuit elements function properly with battery voltage | Input DC voltage to the converter and measure the output DC voltage before the LEDs (with LEDs disconnected) | Completed
Reggie | Converter Output | Converter output powers LED lights | Input DC voltage to the converter with the LEDs connected | Completed
Colton | AC-DC Conversion Test | 2-20VAC is rectified to corresponding DC with < 0.1 V output ripple | Input 3 phase AC voltages and measure corresponding output | Completed
Colton | DC-DC Conversion Test | 6-20VDC is converted to set DC voltage | Input various DC voltages and measure corresponding output | Completed
Responsible Engineer(s) | Test Name | Validation Requirements | Methodology | Status
Colton | Rectifier and Converter Connection Test | Voltage outputs to set DC voltage | Input 3 phase AC voltage to rectifier and measure output DC voltage of converter | Completed
Peter, Colton & Max | Charge Batteries Test | Wind-Power is correctly charging the battery bank with appropriate switching maneuvers | Use wind-turbine to output power, measure if battery capacity has gone up | Completed
Peter, Reggie & Max | Power Output Test | Battery bank is used to power the load with appropriate switching maneuvers | Measure voltage and current at output when battery switches to determine proper switching of power. | Completed
Peter | Input/Output Test | Switch correctly transfers input power to output | Measure voltage and current at the load of the switch and compare with expected current and voltage values | Completed
Peter | Switch Validation | The switch correctly switches between outputs | Input signals from microcontroller and test combination of expected inputs/outputs and verify with voltage and current measurements. | Completed
Maxwell | Battery Capacity Monitor | System is able to successfully track the capacity of the battery | Inputing a voltage and current source into the system or by testing with the actual batteries to see if it can accurately track how much charge is left | Completed
Responsible Engineer(s) | Test Name | Validation Requirements | Methodology | Status
Maxwell | Display Power Generated and Power Usage | System is able to display the power generated from the Wind Turbine, and the power used by the building | Similair to the battery capacity portion there needs to be a voltage and current source to test if this portion is working correctly. | Completed
Maxwell | Dispaly Battery Health | System will be able to calcualte the battery health each battery and display this information to the user allowing them to know if they should replace the battery soon or not | Similair to the battery capacity portion there will need to be a current source to replicate the usage and flow of charge through a battery and seeing if it is able to accurately calcualte the health of said battery. | Removed
Maxwell | Website for System Monitoring | Website is acessible and cleanly displays information about the entire system | Once other parts of the systems are setup the website should be able to correctly display infomration to the user | Completed
Maxwell | Output Signal for Switch Controller | System will have triggers for specific cases of when each battery should be used or charged. Further implementation will be done in 404 | Once connected with the charge and switch controller check that the system is correctly outputting signals to the controller and that the controller is preforming the correct result | Completed
Full Team | Full System Test | Wind-Power is used to charge the battery bank, Monitor sends signals to switching circuits, switch controller outputs correct path, battery power is used by inverter and converter to power the load | Charging: Input power from wind turbine and signals from MCU, then measure and compare voltage and current. Discharging: Power laptop charger and phone charger, verify with voltage and current measurements | Completed

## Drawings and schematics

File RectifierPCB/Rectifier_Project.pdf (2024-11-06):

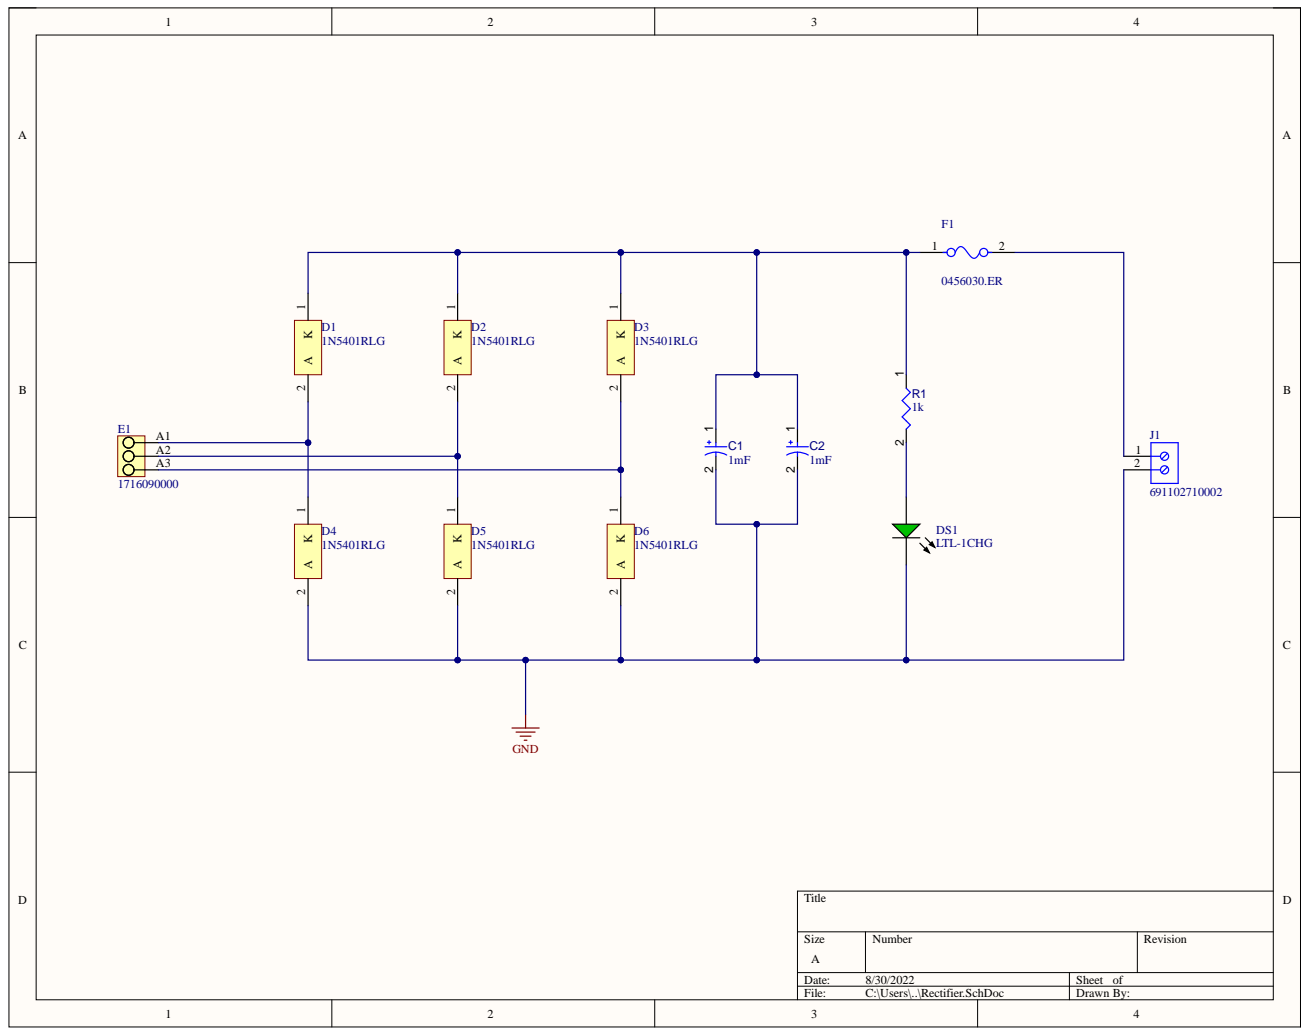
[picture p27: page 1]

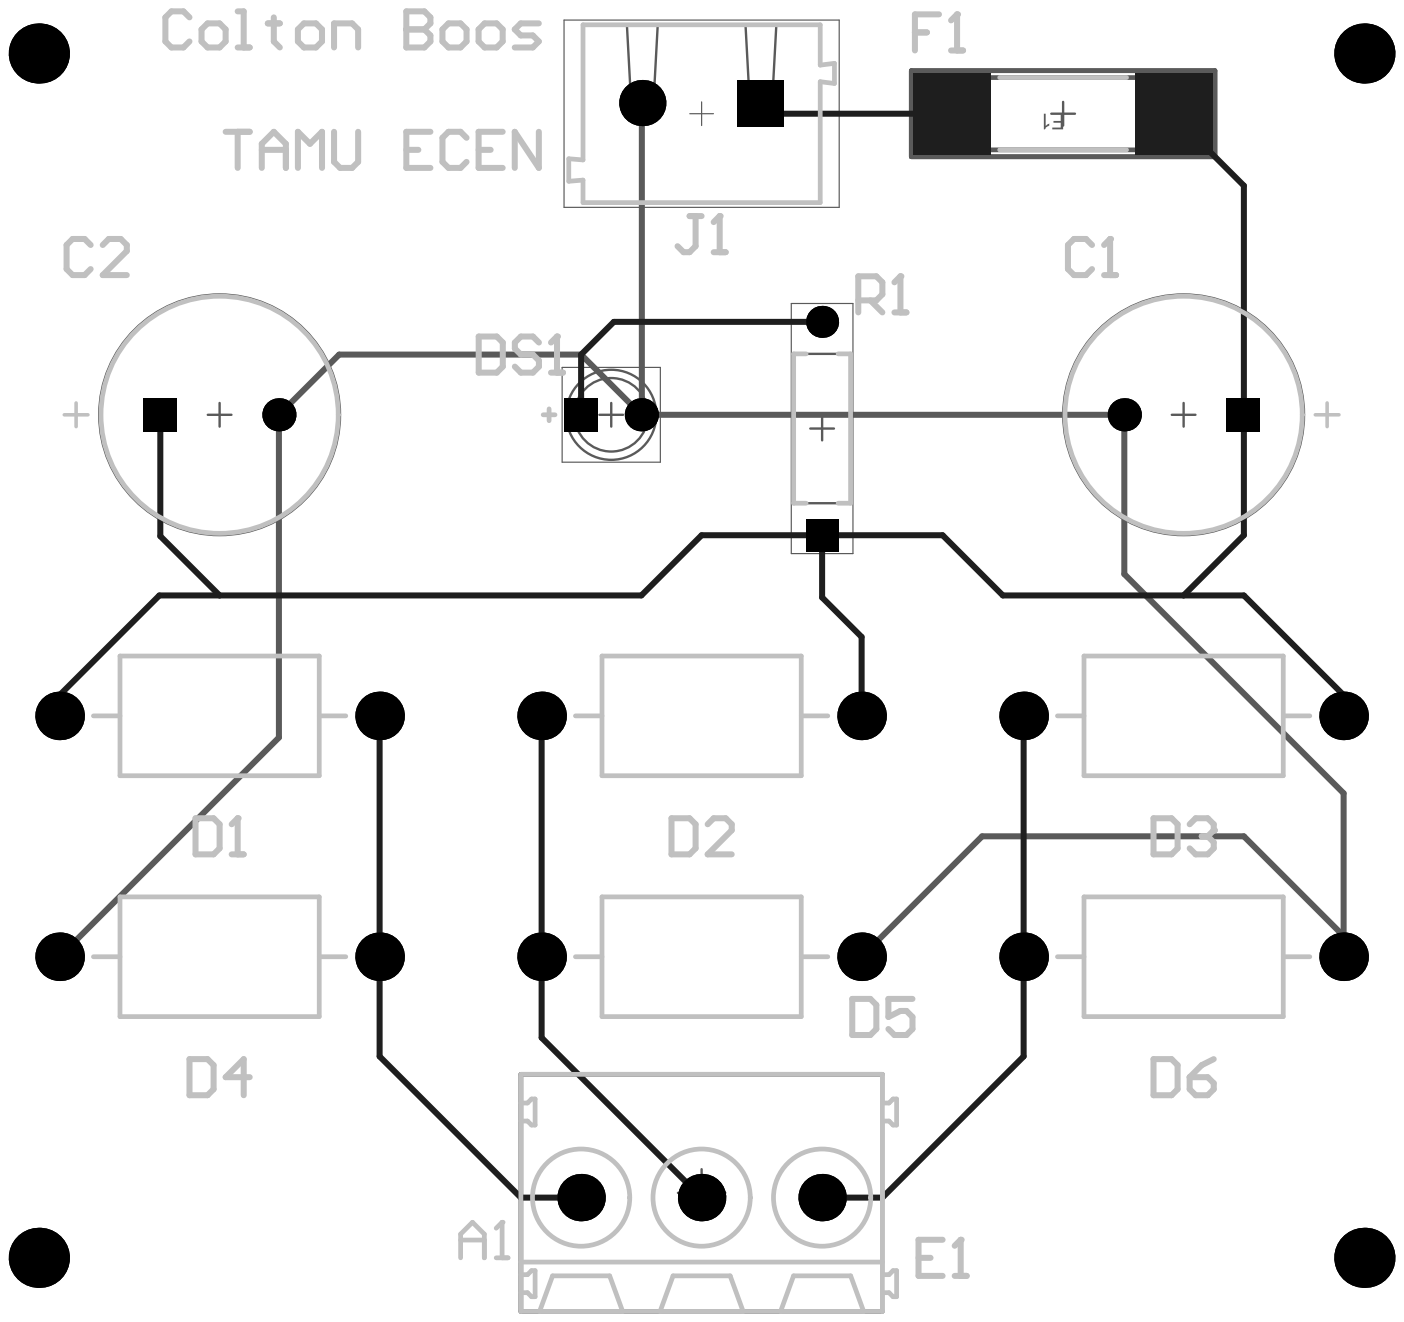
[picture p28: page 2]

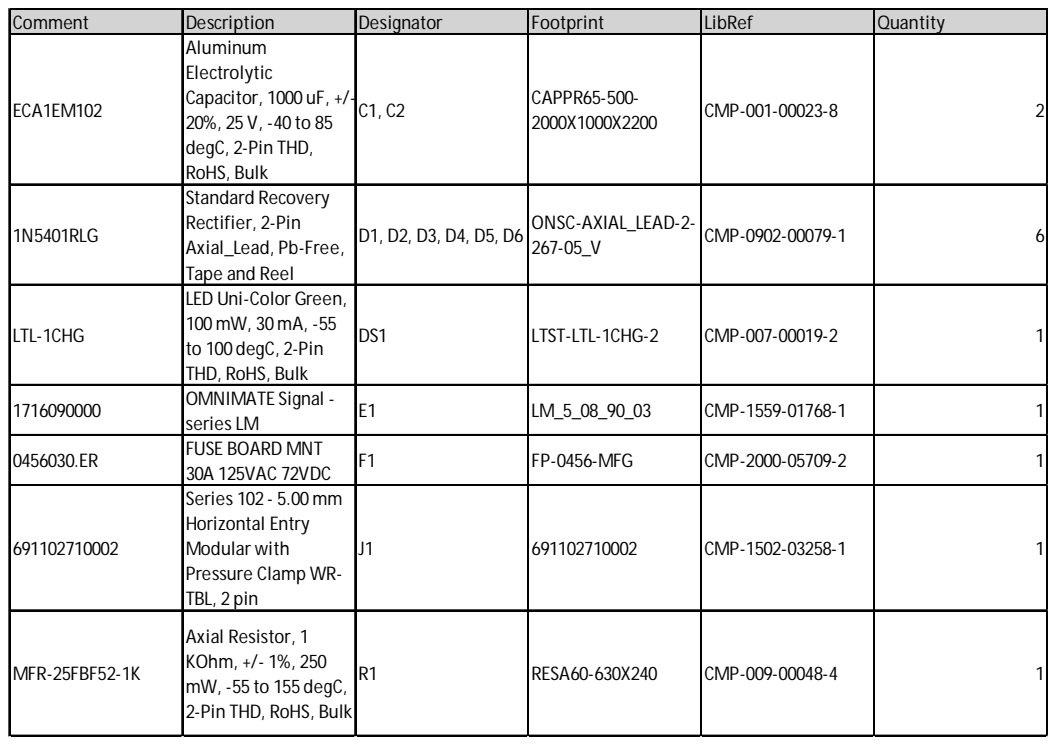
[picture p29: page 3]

Comment | Description | Designator | Footprint | LibRef | Quantity
ECA1EM102 | Aluminum Electrolytic Capacitor, 1000 uF, +/-20%, 25 V, -40 to 85 degC, 2-Pin THD, RoHS, Bulk | C1, C2 | CAPPR65-500-2000X1000X2200 | CMP-001-00023-8 | 2

1N5401RLG | Standard Recovery Rectifier, 2-Pin Axial_Lead, Pb-Free, Tape and Reel | D1, D2, D3, D4, D5, D6 | ONSC-AXIAL_LEAD-2-267-05_V | CMP-0902-00079-1 | 6

LTL-1CHG | LED Uni-Color Green, 100mW, 30mA, -55 to 100 degC, 2-Pin THD, RoHS, Bulk | DS1 | LTST-LTL-1CHG-2 | CMP-007-00019-2 | 1

1716090000 | OMNIMATE Signal -series LM | E1 | LM_5_08_90_03 | CMP-1559-01768-1 | 1

0456030.ER | FUSE BOARD MNT 30A 125VAC 72VDC | F1 | FP-0456-MFG | CMP-2000-05709-2 | 1

691102710002 | Series 102 - 5.00mm Horizontal Entry Modular with Pressure Clamp WR-TBL, 2 pin | J1 | 691102710002 | CMP-1502-03258-1 | 1

MFR-25FBF52-1K | Axial Resistor, 1 KOhm, +/- 1%, 250 mW, -55 to 155 degC, 2-Pin THD, RoHS, Bulk | R1 | RESA60-630X240 | CMP-009-00048-4 | 1

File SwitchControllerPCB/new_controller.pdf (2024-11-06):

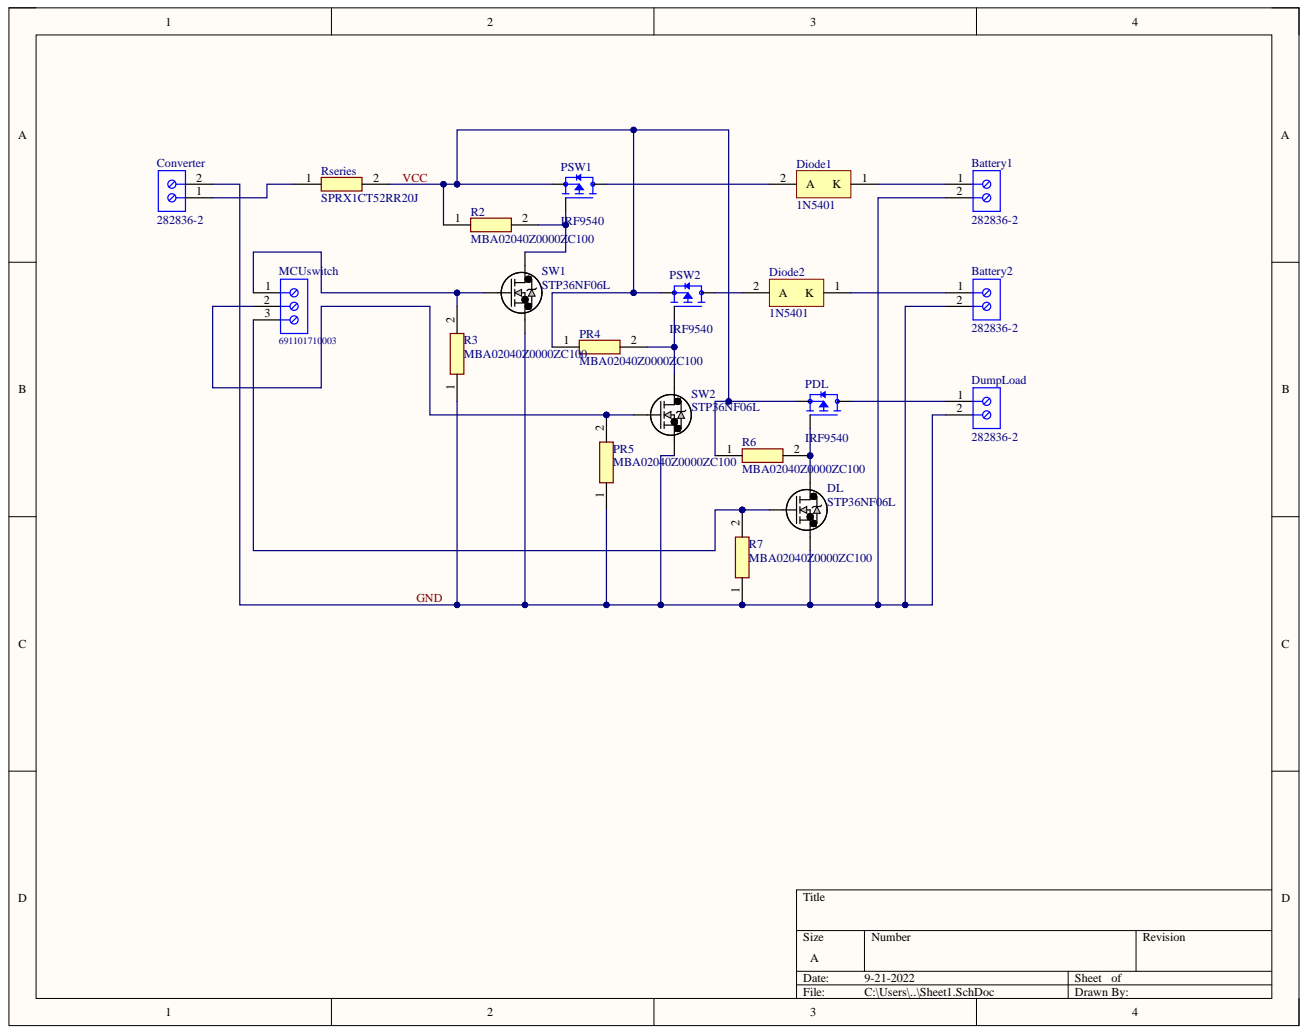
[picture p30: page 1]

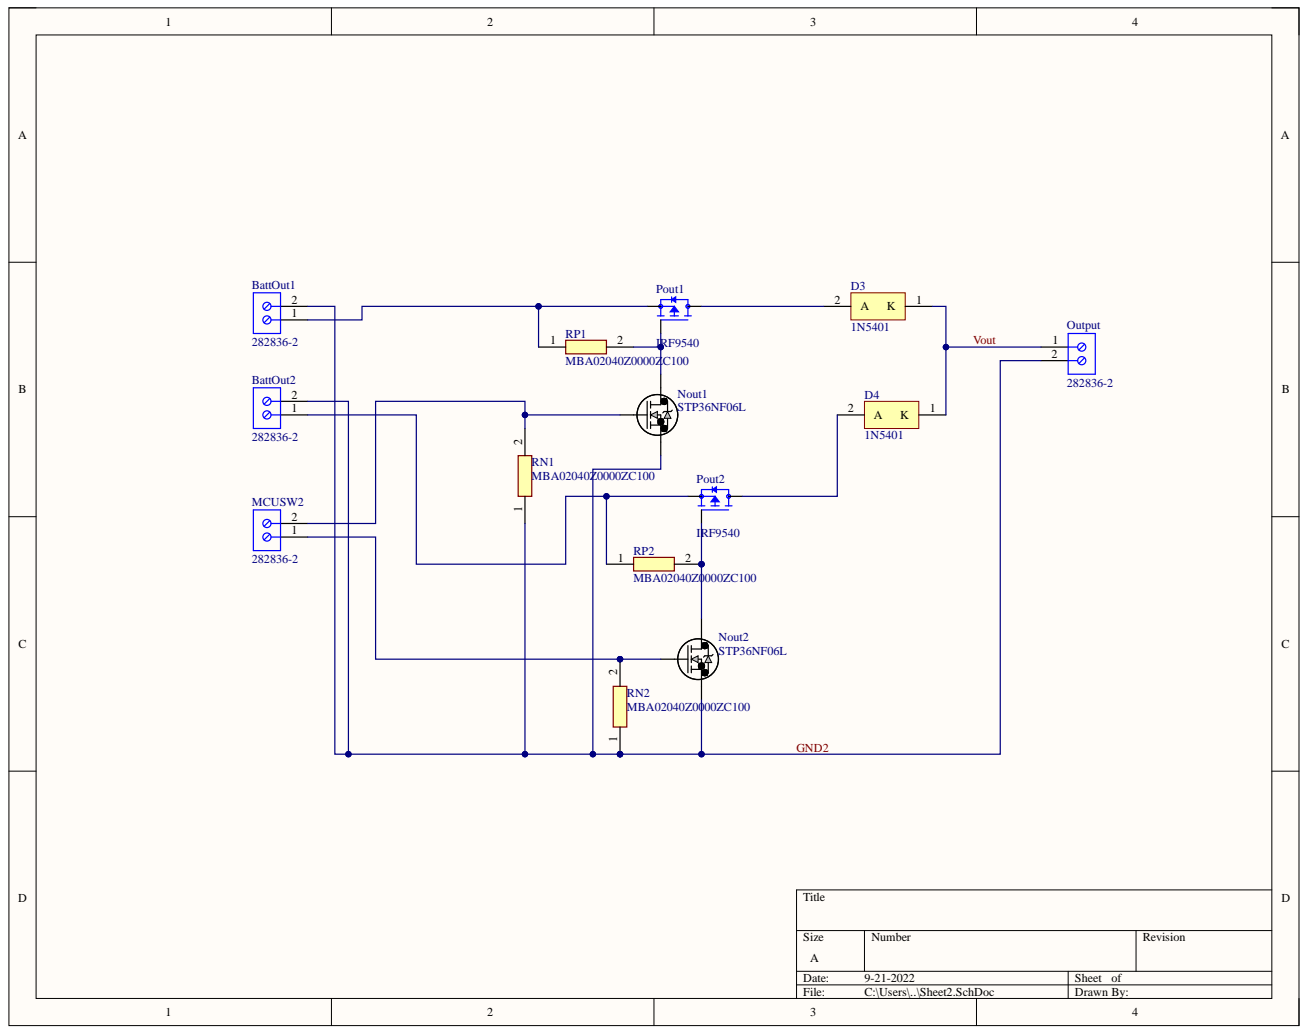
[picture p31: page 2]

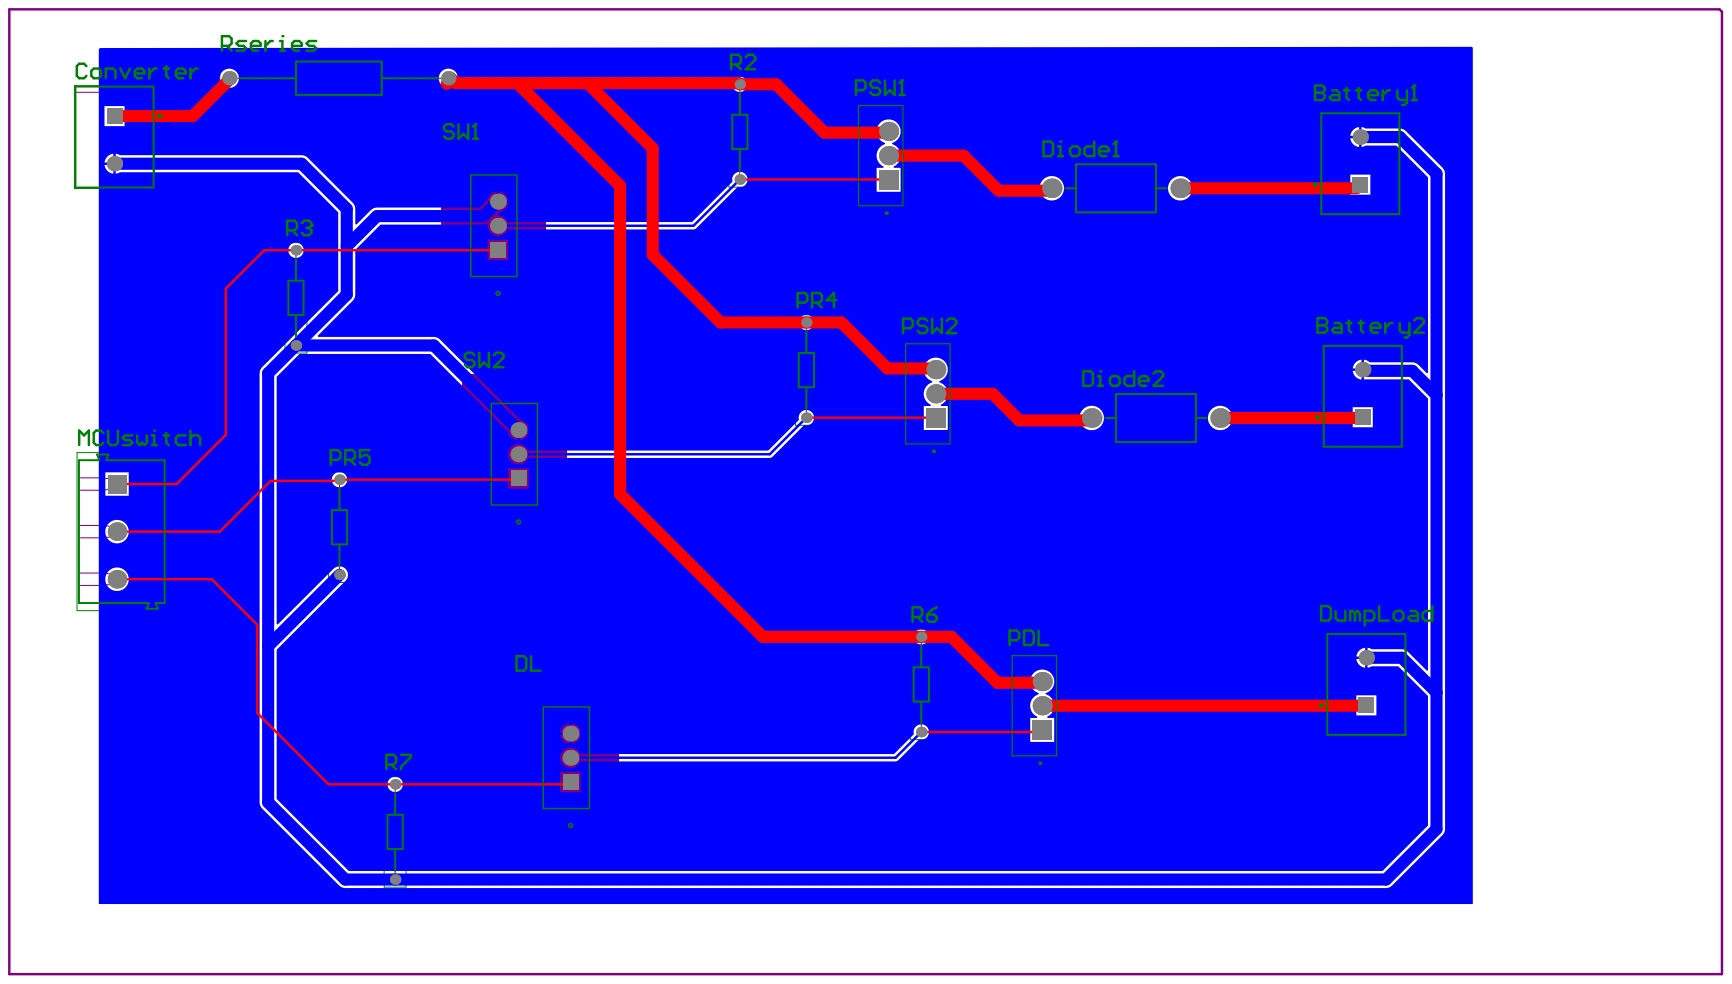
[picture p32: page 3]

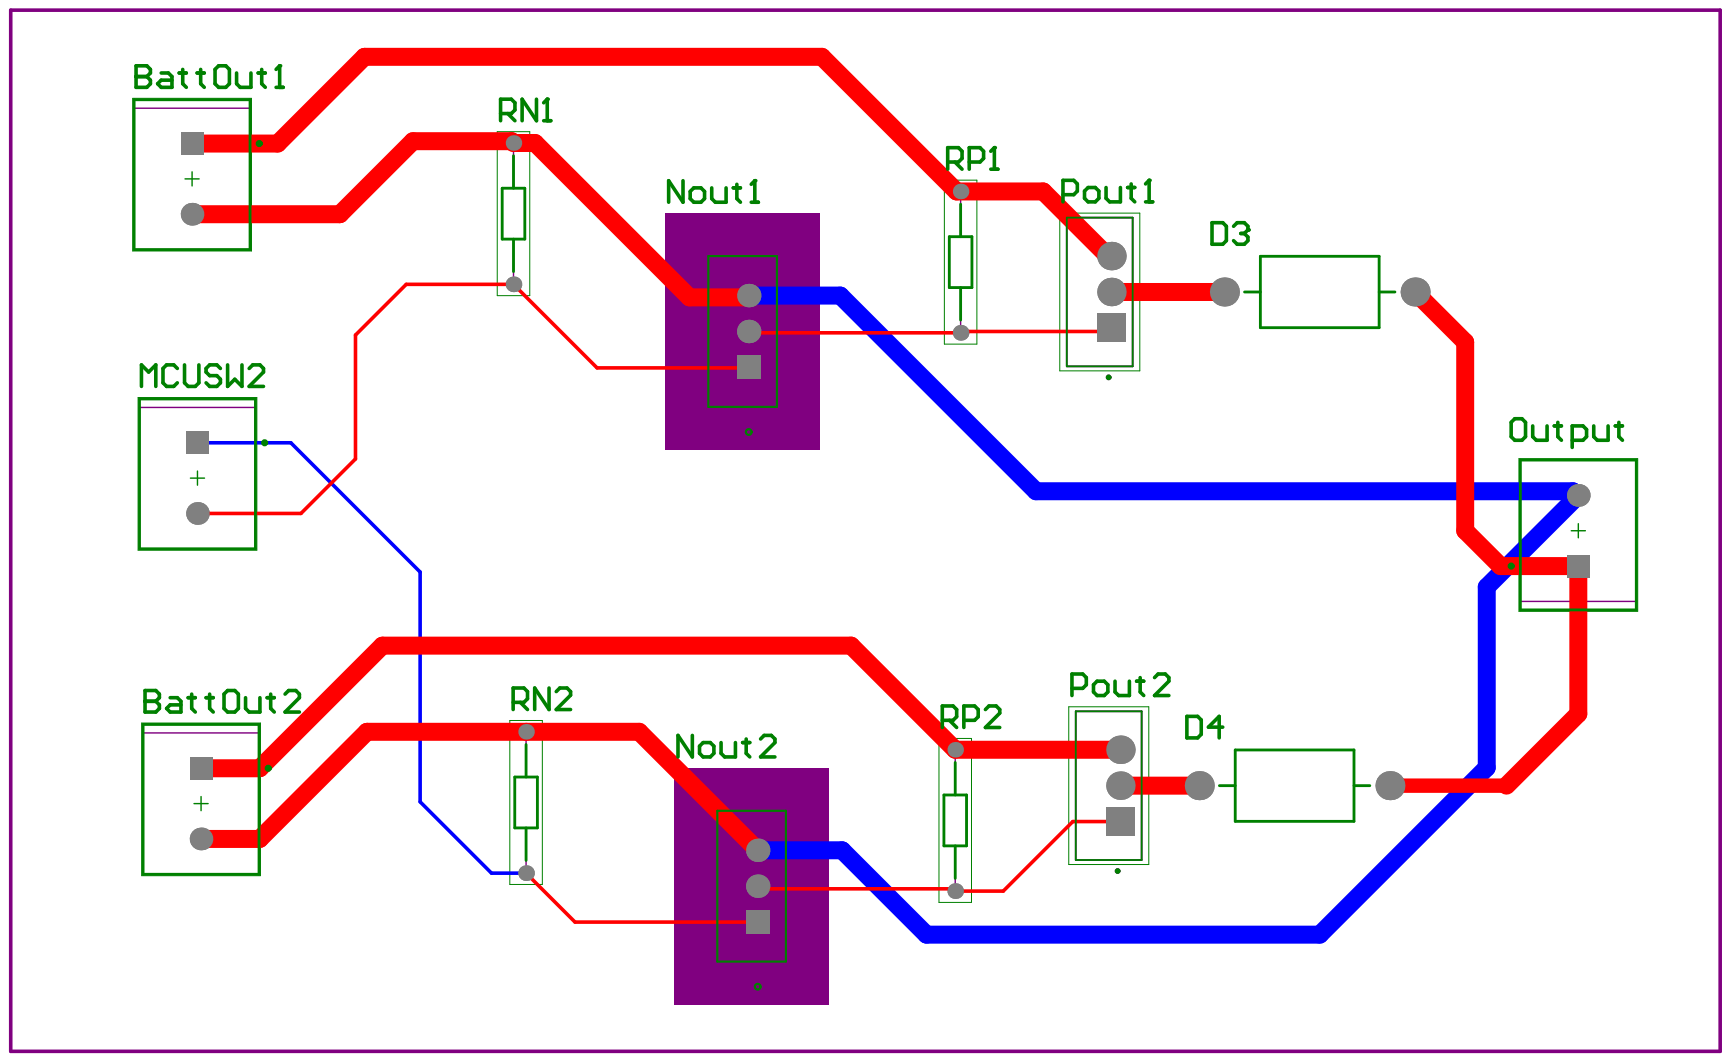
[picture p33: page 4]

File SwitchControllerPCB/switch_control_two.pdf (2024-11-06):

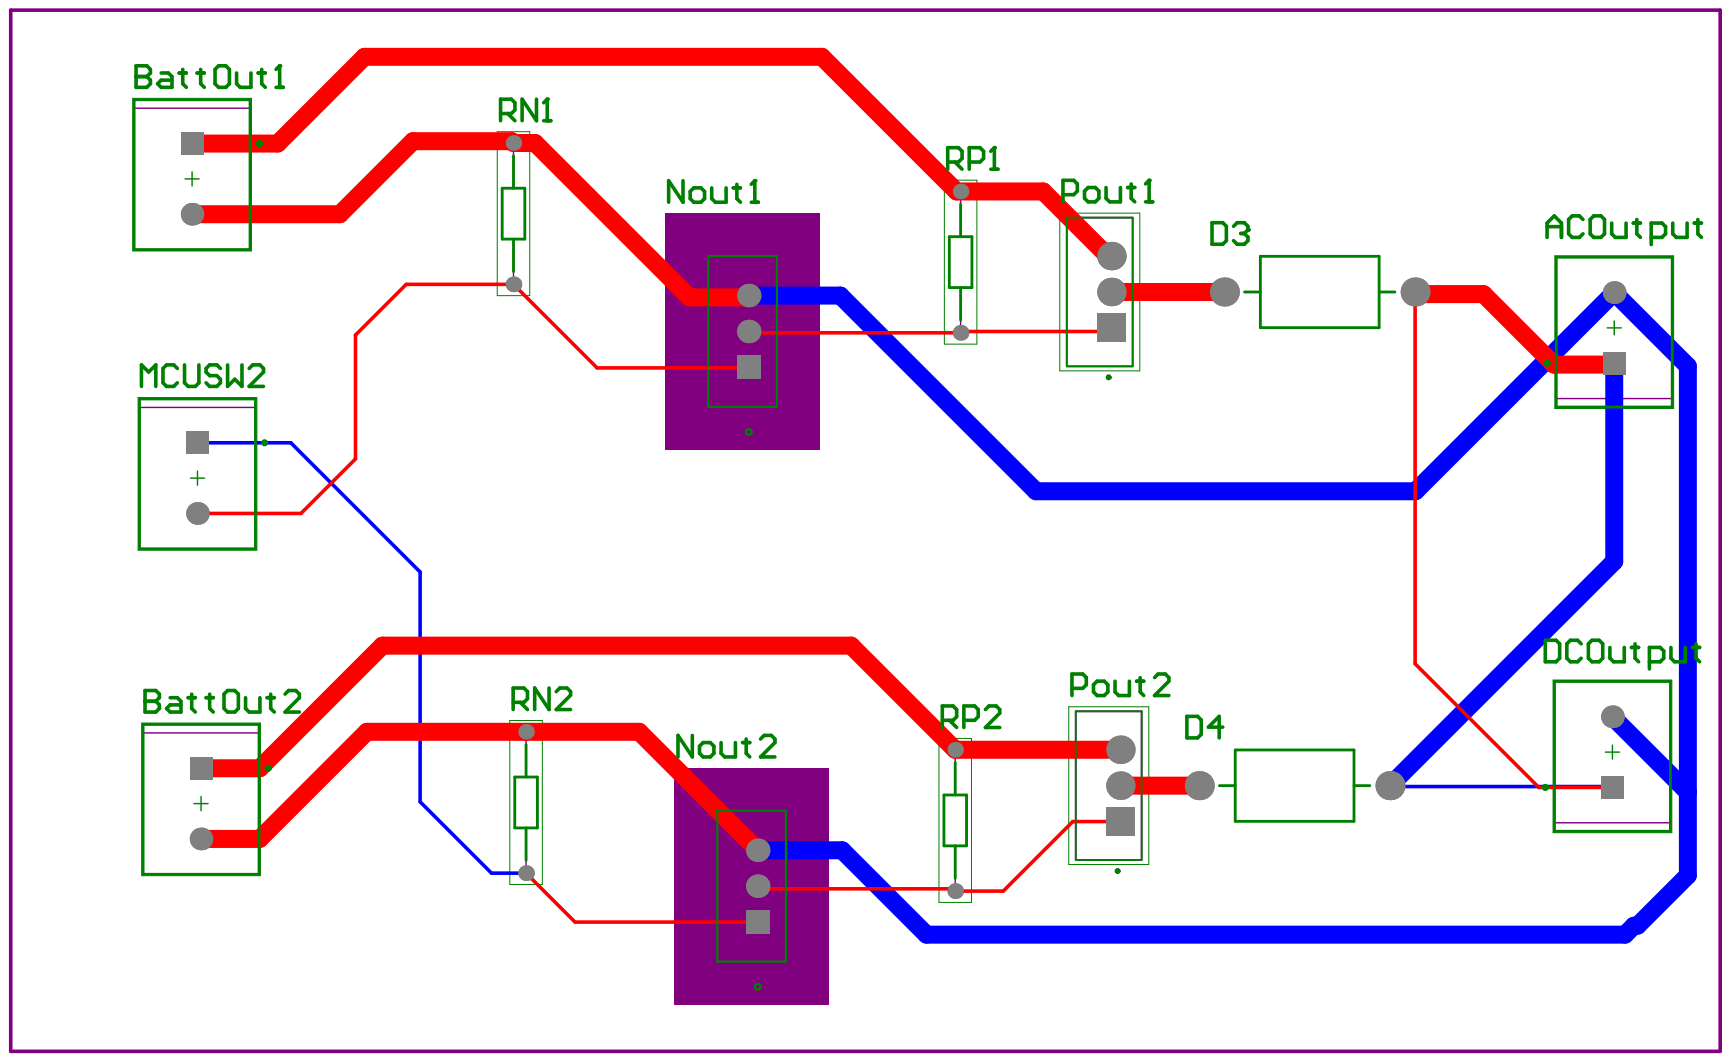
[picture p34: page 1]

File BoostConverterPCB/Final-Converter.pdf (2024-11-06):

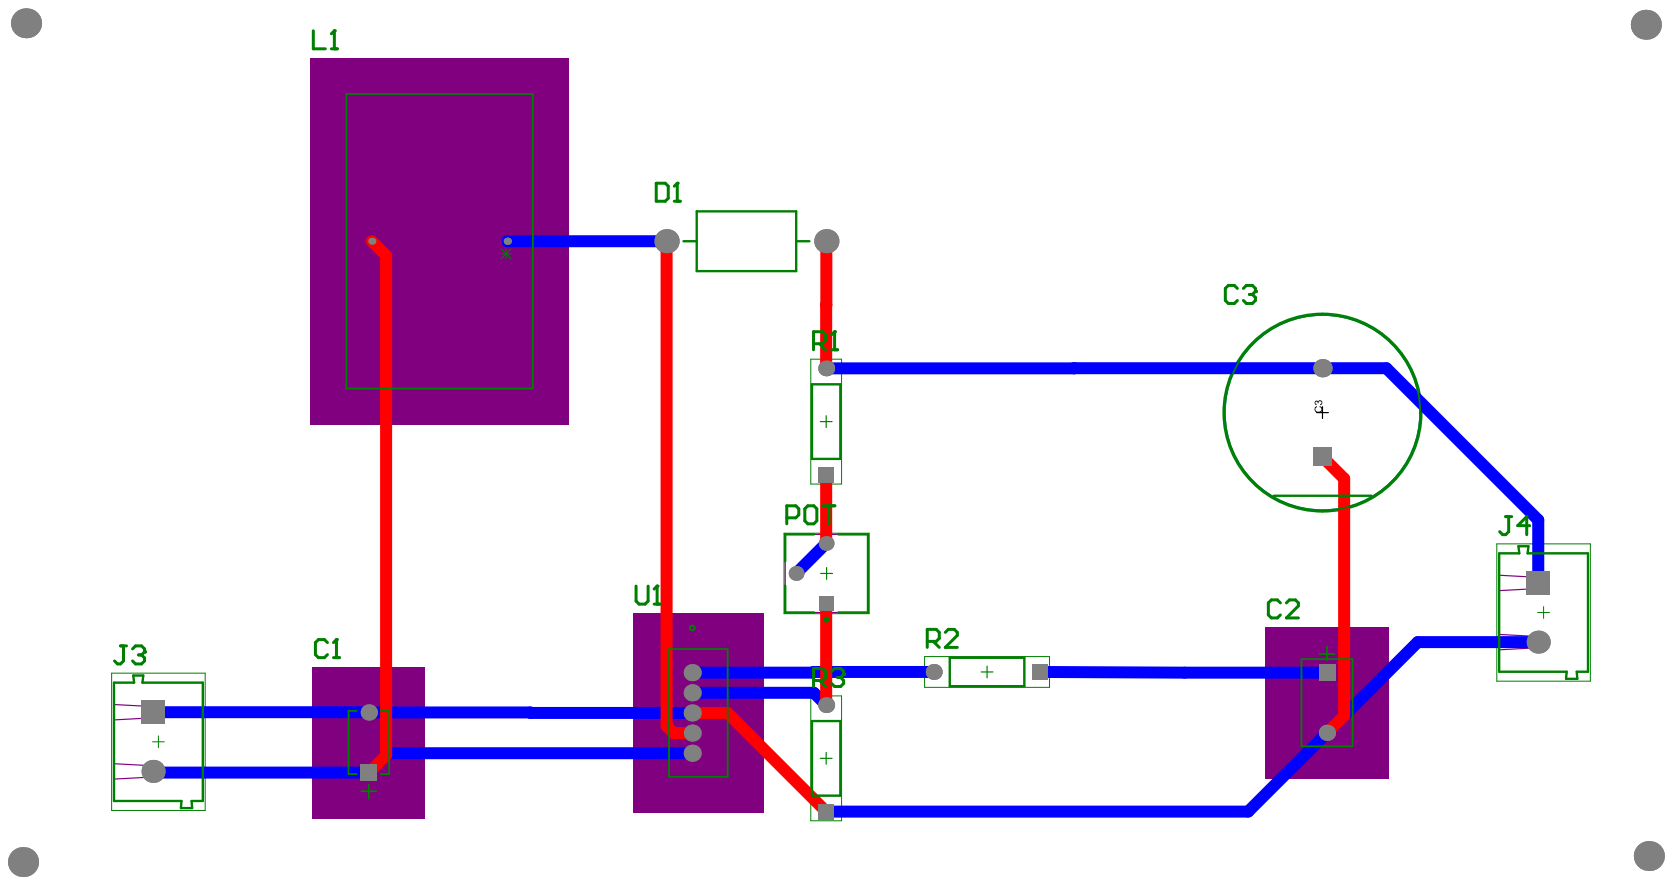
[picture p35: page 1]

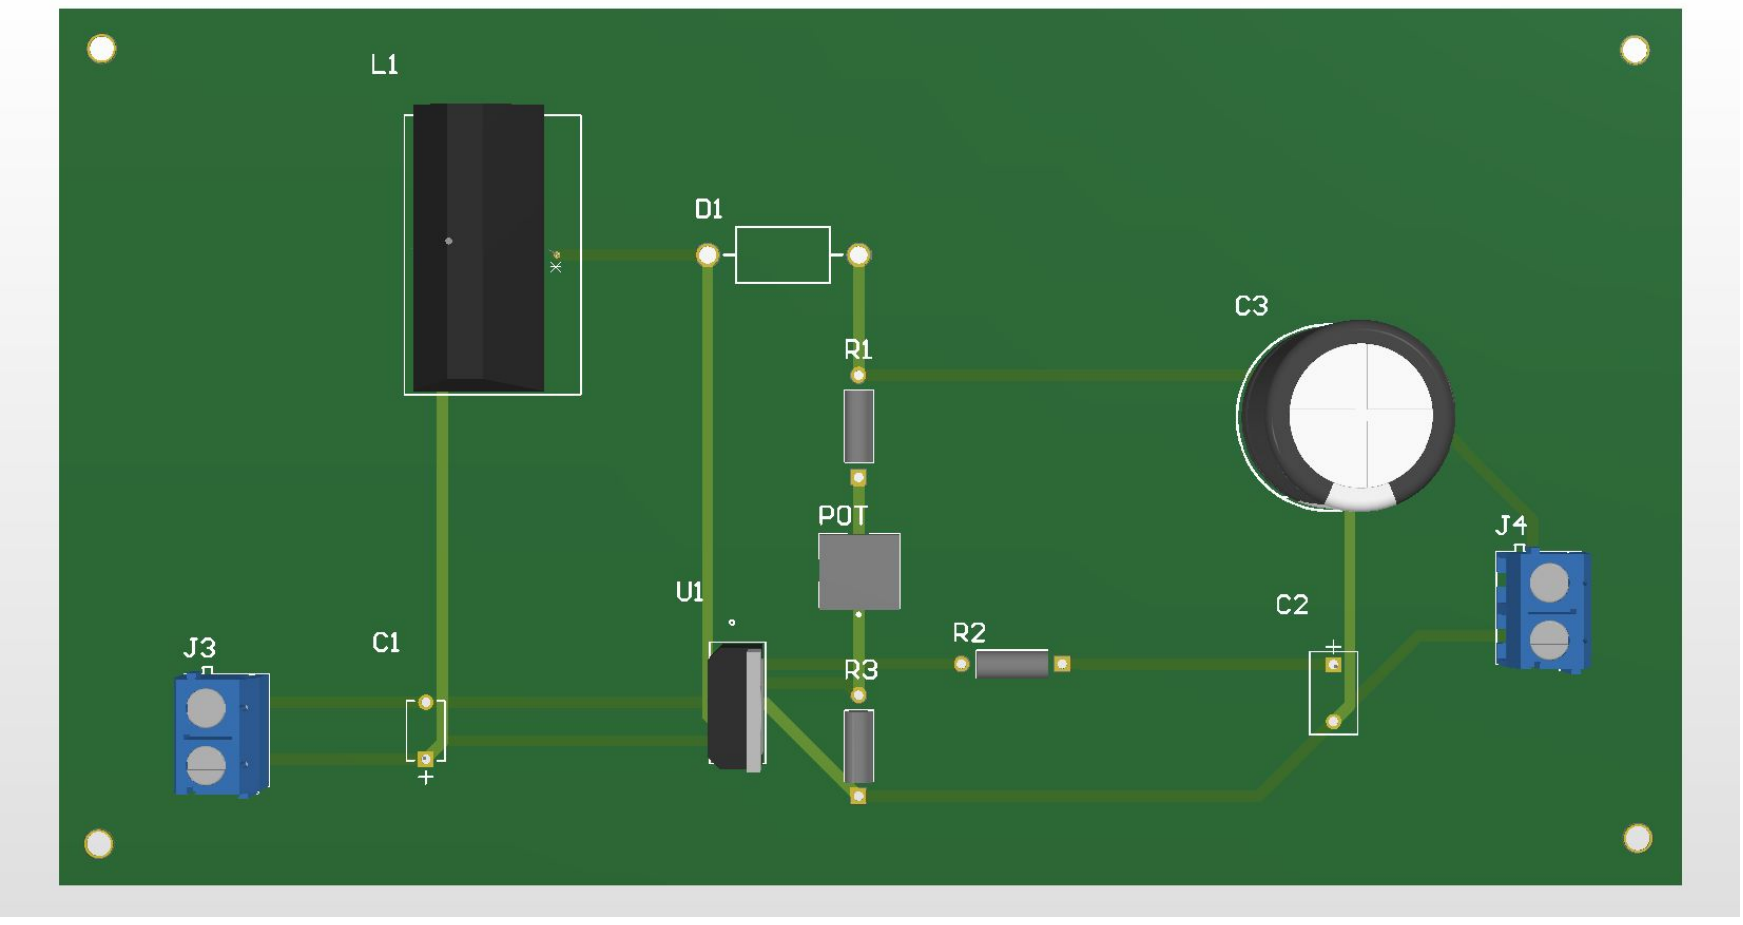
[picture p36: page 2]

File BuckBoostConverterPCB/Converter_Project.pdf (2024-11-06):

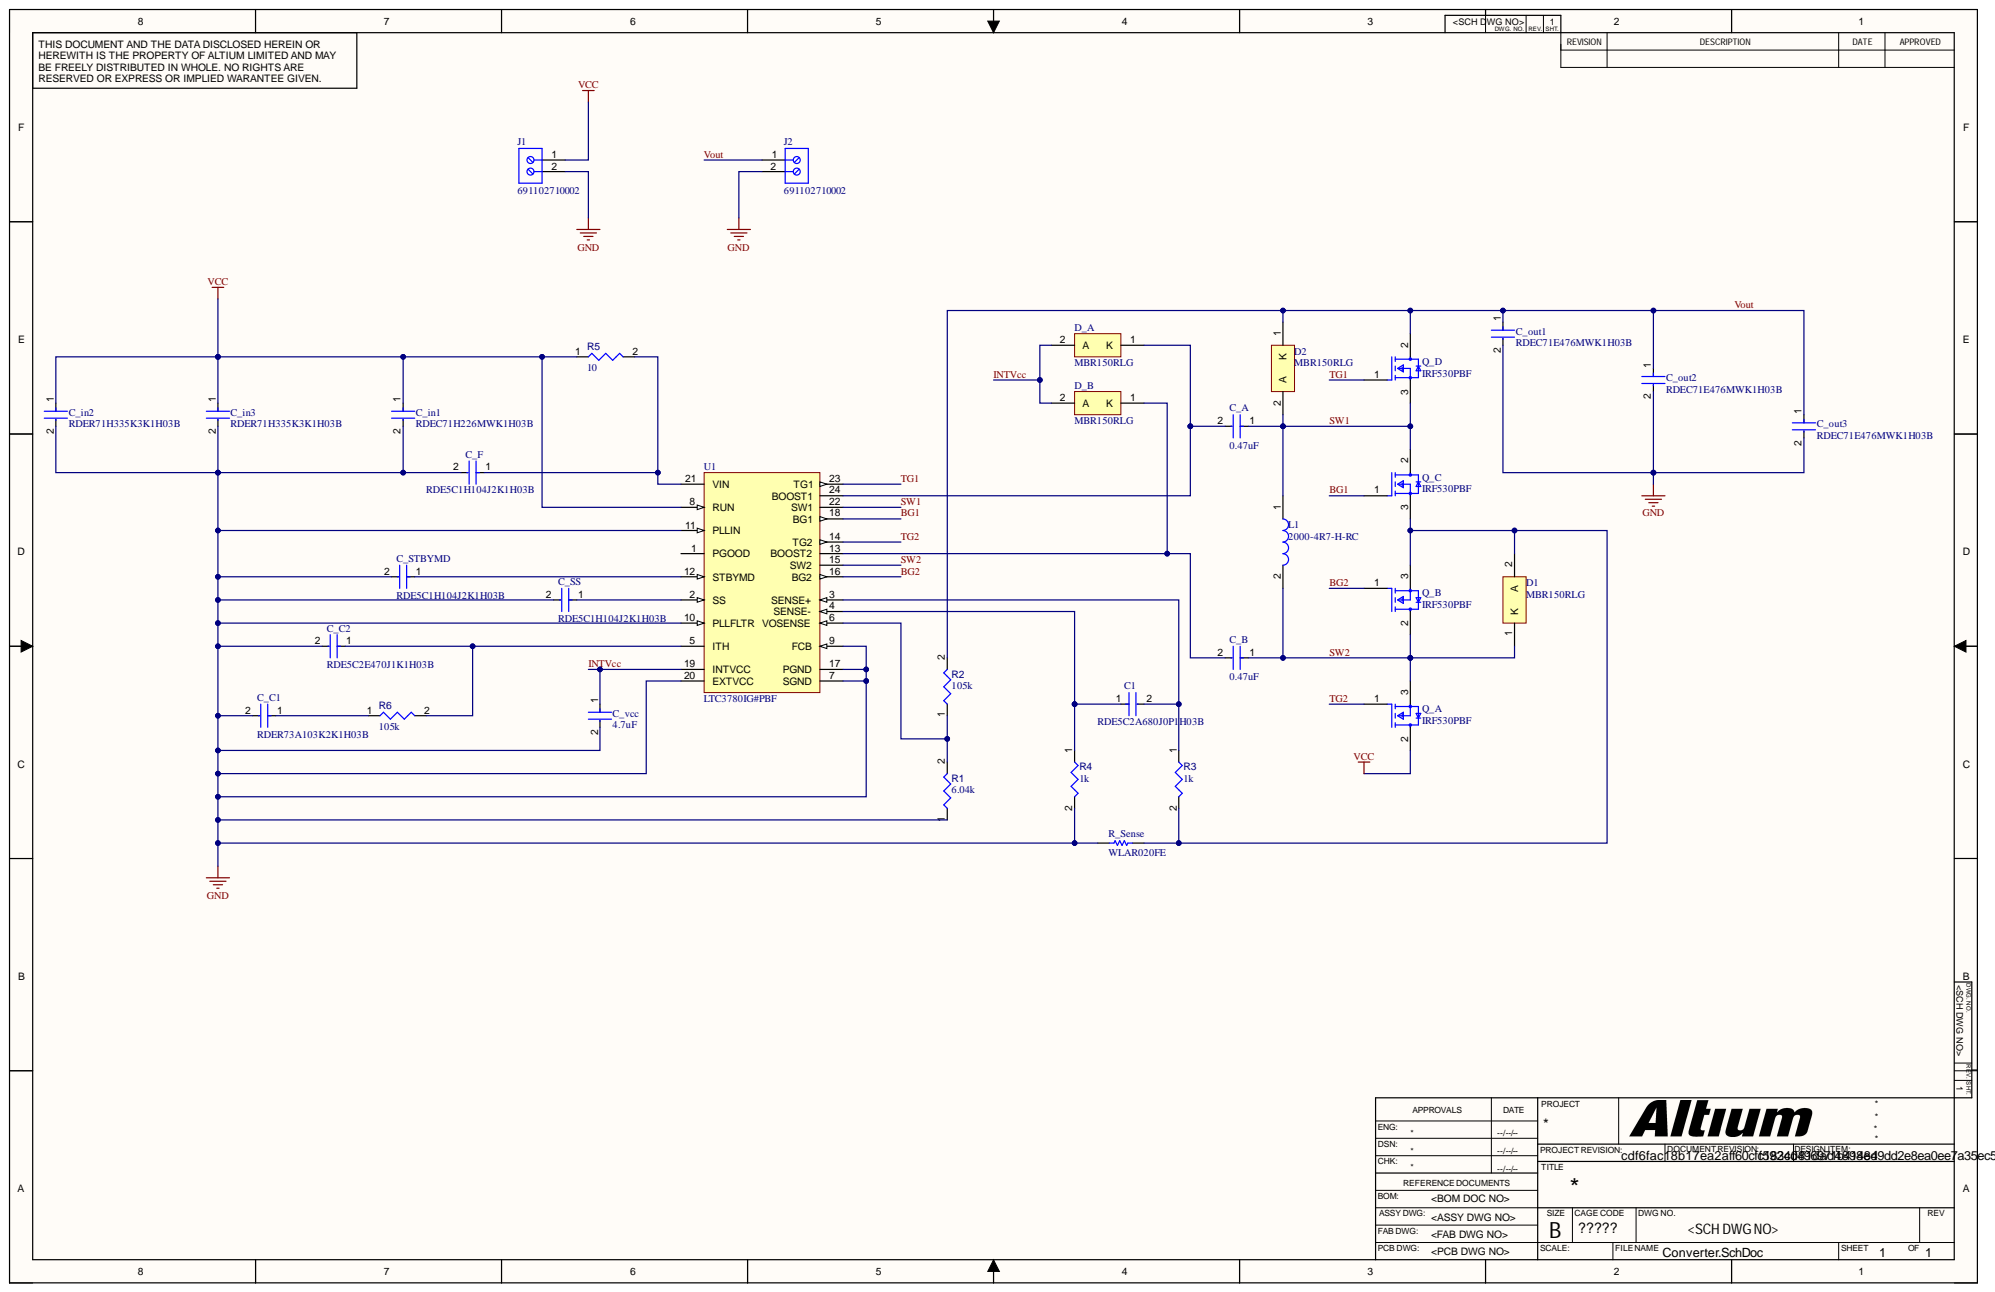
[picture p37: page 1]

T H I S D O C UME N T A N D T H E D AT A D I S C L O S E D H E R E I N O R H E R EWI T H I S T H E P R O P E R T Y O F A LT I UM L IMI T E D A N D MAY B E F R E E LY D I S T R I B U T E D I N WH O L E . N O R I G H T S A R E S O S S O G R E E R V E D R E X P R E R IMP L I E D WA R A N T E E I V E N . | V C C | RE V I S I O N | DE SCRI PT I O N | DAT E | A P PROV E D

REV. SHT. DWG. NO.

A P PROV A L S | DAT E | PROJE CT * | ****

ENG : | --/--/--
** DSN: | --/--/--

PROJECT RE VISION : c df6fa c | 1 DOCUM 8 b 1 7 ENT RE e a 2 a VISION ff 6 0 c f : cf51 98 23 4c | d04891 DE SIGN IT 6d9a7d14b8491 E M : 84 e8 d4 9 d d 2 e 8 e a 0 e e | 7

CHK : * | --/--/--

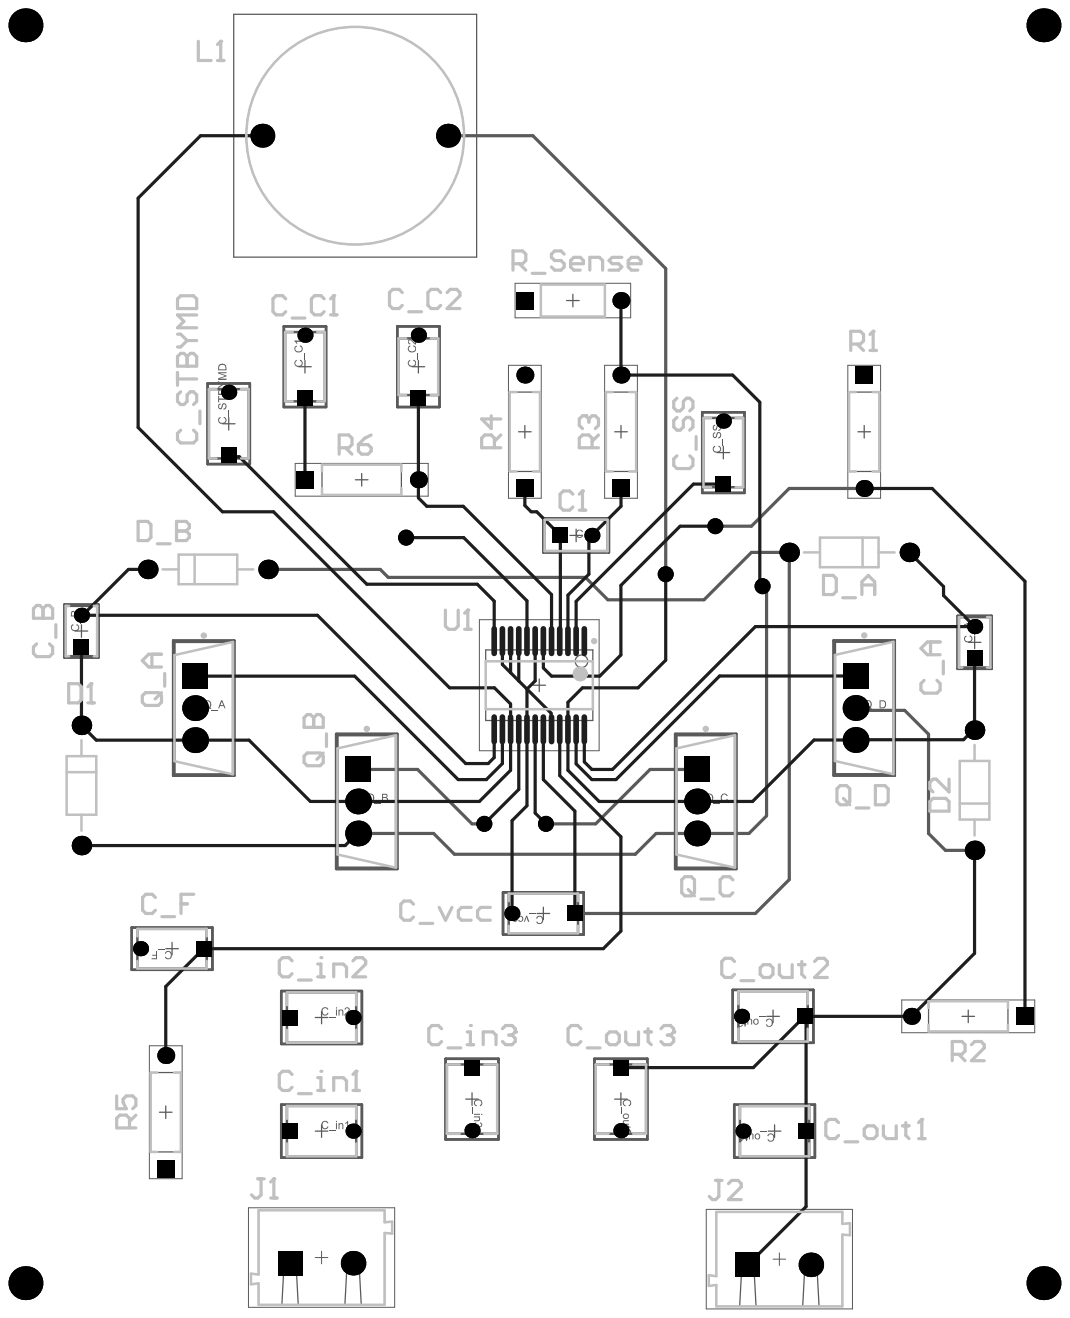
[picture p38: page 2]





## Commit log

2024-11-06 Part of Windpowered Building Repo Copy
    [BBConverter.PrjPcb, CONVERTER_ALTIUM.SchDoc, Converter-PCB.PcbDoc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]
2024-11-06 Other part of the Repo
    Programming parts were done by me, while the others were done by my teammates Colton, Reggie, and Peter
    [404 Execution Plan.xlsx, 404 Validation Plan.xlsx, Copy of new_switch_control_one.PcbDoc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]
